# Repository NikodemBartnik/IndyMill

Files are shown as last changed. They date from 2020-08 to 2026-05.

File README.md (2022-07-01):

IndyMill image

IndyMill is an open source DIY CNC machine that is mostly made out of metal. It was designed with simplicity and minimalism in mind! 
This project is not aiming to be the most heavy duty CNC machine out there, it is meant to be easy and inexpensive to build so that anyone can get a hand on precise CNC machining in many materials including metal.
Designed by [Nikodem Bartnik](https://www.youtube.com/nikodembartnik). 

Here are just some of the features of this machine:

  - Aluminium profiles (2080 and 2040)
  - Compatible with Nema17 and Nema23 on X and Y axis (without redesigning a plate Z axis is only compatible with Nema23)
  - Made with ball screws, linear rails and 6mm steel plates to ensure rigidity
  - Can be easily scaled up, you just need to use longer profiles, ballscrews and linear rails

***

### You can find more info at [Indystry.cc](https://indystry.cc/)

***

## Open Source
This machine is open source, so above you can find all of the files that you need to build it. You can also check out videos below to see the build process. As for now, the machine was tested with various kinds of wood, MDF, acrylic and aluminium. It is able to machine all of those materials even with a small 500W spindle.
You can also find more information on my website: [Indystry.cc](https://indystry.cc/indymill/)

## Parts

You can find parts list in PDF or XLSX above but you can also find it here:
  - At [indystry.cc/indymill](https://indystry.cc/indymill) you can find a full table with all needed parts
  - [Google Drive Parts List](https://docs.google.com/spreadsheets/d/19kC1wDViL0N2BjQgnNMfYSCzLNLKAHwQCY5Ngf8wU5I) here you can find an online parts list 
  - You can buy some of the parts on my [store](https://indystry.cc/store/)

## Videos

IndyMill Final test (https://www.youtube.com/watch?v=5jFCecZdbGs)
500W spindle dust shoe (https://www.youtube.com/watch?v=k00IwDHeDQE)
Best upgrades to a CNC machine (https://www.youtube.com/watch?v=VLe03TqoPkM)
Making a CNC drawer (https://www.youtube.com/watch?v=OfrpIvfrLAs)

## Build Instruction
This project is open source so you can find all the files that you need to build it above for free. You can easily build it just by taking a look at some images on my website and my videos.
But if you would like to get a PDF instruction that simplifies the build process, you can easily print it put or it on a smartphone or computer. You can get one through link below and at the same time support my projects! You don't need it but it may help a little :)

### https://gum.co/indymill

### Todos

 - Design a better, bigger cable chain

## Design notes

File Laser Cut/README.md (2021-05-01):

# Laser Cut

These plates can easily be laser cut from steel or aluminium. Steel is  a prefered material as it is stronger and usually cheaper to laser cut. You must shop around for the best price in your country. Also make sure that they are able to cut small holes with a laser, some companies say it's impossible but with a good laser it is easily doable. 
You can also make them on your own with a CNC machine or any other way you want, if you need dimensions just import DXF files to your CAD software and measure whatever you need.
You can also buy the plates in my [store](https://indystry.cc/store/).

DXF files are in `mm`.

| Part | What it looks like |
| --- | --- |
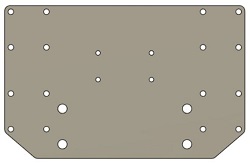
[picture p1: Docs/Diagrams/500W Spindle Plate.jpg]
500W Spindle Plate
| [500W Spindle Plate](500W%20Spindle%20Plate.dxf) |  |
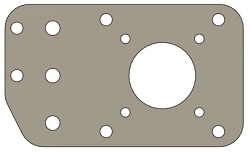
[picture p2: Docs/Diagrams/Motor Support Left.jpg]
Motor Support Left
| [Motor Support Left](Motor%20Support%20Left.dxf) |  |
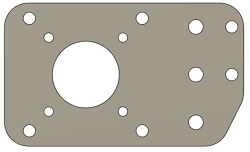
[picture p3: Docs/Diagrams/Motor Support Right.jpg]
Motor Support Right
| [Motor Support Right](Motor%20Support%20Right.dxf) |  |
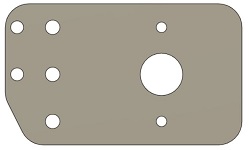
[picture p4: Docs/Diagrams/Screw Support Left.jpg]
Screw Support Left
| [Screw Support Left](Screw%20Support%20Left.dxf) |  |
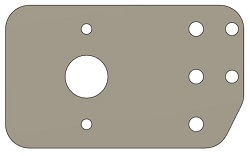
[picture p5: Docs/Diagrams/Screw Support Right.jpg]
Screw Support Right
| [Screw Support Right](Screw%20Support%20Right.dxf) |  |
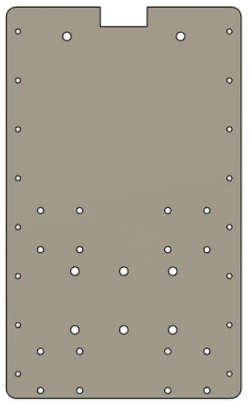
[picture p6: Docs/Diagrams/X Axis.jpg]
X Axis
| [X Axis](X%20Axis.dxf) |  |
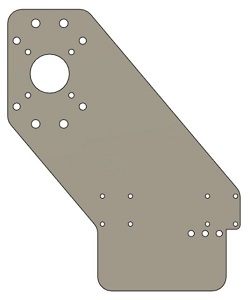
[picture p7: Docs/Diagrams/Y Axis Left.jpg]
Y Axis Left
| [Y Axis Left](Y%20Axis%20Left.dxf) |  |
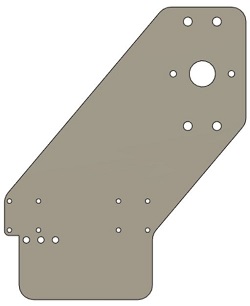
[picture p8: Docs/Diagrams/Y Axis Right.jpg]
Y Axis Right
| [Y Axis Right](Y%20Axis%20Right.dxf) |  |
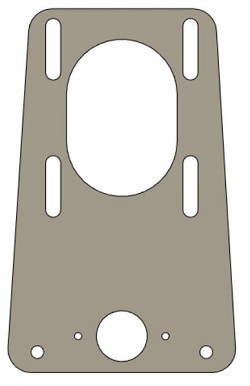
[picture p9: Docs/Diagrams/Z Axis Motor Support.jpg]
Z Axis Motor Support
| [Z Axis Motor Support](Z%20Axis%20Motor%20Support.dxf) |  |
| [Z Axis Rail Support1](Z%20Axis%20Rail%20Support1.dxf) | Z Axis Rail Support1 |
| [Z Axis Rail Support2](Z%20Axis%20Rail%20Support2.dxf) | Z Axis Rail Support2 |

Sometimes people ask me if it is possible to make those plates with different material than metal. It should be possible with thick plywood but obviously machine is not going to be that rigid. 3D printing those plates is most likely not a good idea.
Keep in mind I never tried making those plates out of wood or 3D printing.

Thanks to nice plates images and table to @carlpaton

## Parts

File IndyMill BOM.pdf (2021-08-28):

# List of parts for IndyMill by Nikodem Bartnik

Electronics

Part name | Quantity | BangGood | Aliexpress | Amazon | Comment
Nema23 Stepper motor | 4 | https://bit.ly/2Y0BnrI | https://bit.ly/3iBTGvk | https://amzn.to/3DeE641
IndyShield | 1 | - | - | - | You can buy it here: https://indystry.cc/store/
TB6600 stepper drivers | 4 | https://bit.ly/33VQFSs | https://bit.ly/2PSt2lG | https://amzn.to/3gB2Ycu
Arduino UNO | 1 | https://bit.ly/3gVqtLs | https://bit.ly/2FeDxxo | https://amzn.to/3zo98Uw
Power supply | 1 | https://bit.ly/30RaqZA | https://bit.ly/3kJOtDu | https://amzn.to/2WkwLPR
AC Socket | 1 | https://bit.ly/30Tk2mr | https://bit.ly/30REsfK | https://amzn.to/3mveo5k
Cables | - | https://bit.ly/2PQ2qlc | https://bit.ly/3kH9TBh | -
4 pin connectors | 4 | https://bit.ly/30UUpSi | https://bit.ly/3am7dUU | https://amzn.to/3zm0OVw | I used that to connect stepper motors through electronics case, use other connectors if you want
500W Spindle | 1 | https://bit.ly/3gVpcnx | https://bit.ly/3iCR4NJ | https://amzn.to/3kqVz0z | Choose a spindle that will work best for you. I recommend 500W spindle for beginners, if you are already experienced or not afraid to go BIG go with 1.5kW spindle (that's some serious power!). For 1.5kW spindle you will also need an inverter.
1.5kW Spindle | 1 | https://bit.ly/3kGN4O7 | https://bit.ly/2PMiLHE | https://amzn.to/3mzGw7i
Inverter for 1.5kW Spindle | 1 | https://bit.ly/2E0aHQO
Mechanics
Part name | Quantity | BangGood | Aliexpress | Amazon | Comment
Aluminium profile 20x40 mm 600 mm | 2 | https://bit.ly/3iGGfdM | https://bit.ly/30VoyRv | https://amzn.to/3B9BG4G | You will most likely need to buy longer pieces of aluminium profiles and cut them to a proper length,
| | | | | if you want to build, bigger machine you just have to change lengths of those items, everything else
| | | | | stay the same
Aluminium profile 20x40 mm 666 mm | 2 | https://bit.ly/2XYn3QE | https://bit.ly/3kC0ZoJ | https://amzn.to/3B9BG4G
Aluminium profile 20x80 mm 600 mm | 2 | https://bit.ly/2Y03gQL | https://bit.ly/2PRw7Cs | https://amzn.to/3B9BthU
Trapezoidal lead screw 220 mm | 1 | https://bit.ly/2PS5r4C | https://bit.ly/31Nef0Z | https://amzn.to/3zpXgS4 | Buy longer piece of trapezoidal lead screw and cut to 220mm
Ball Screw SFU1605 650 mm | 1 | https://bit.ly/3fR7yQJ | https://bit.ly/33X9uET | https://amzn.to/3mBfTyM
Ball Screw SFU1605 600 mm | 2 | https://bit.ly/2PQIXkg | https://bit.ly/33X9uET | https://amzn.to/3yeHyrH
Linear Rail MGN12 650 mm | 2 | https://bit.ly/2DSsF85 | https://bit.ly/2XY4ADA | https://amzn.to/2UQD0dp | X axis
Linear Rail MGN12 600 mm | 2 | https://bit.ly/2DSsF85 | https://bit.ly/2XY4ADA | https://amzn.to/3yjJ7o4 | Y axis
Linear Rail MGN12 200 mm | 2 | https://bit.ly/2DSsF85 | https://bit.ly/3fWvn9N | https://amzn.to/3zmz3Mj | Z axis
Linear Rail Block MGN12H | 12 | https://bit.ly/3gVz94w | https://bit.ly/3gVSOBm | https://amzn.to/3zmosBh | If you buy each rail with one block you need just 6 additional blocks (the total of 12)
6000RS bearing | 3 | https://bit.ly/30RjJsl | https://bit.ly/30Uv0by | https://amzn.to/3BtqgsX
6201RS bearing | 6 | https://bit.ly/3h7TWSF | https://bit.ly/2E44Tpj | https://amzn.to/2Y0GRWv
608RS bearing | 1 | https://bit.ly/33Wh6Hz | https://bit.ly/2XYrk6t | https://amzn.to/3kvRVCz
8 to 10mm coupler | 3 | https://bit.ly/30SUCoV | https://bit.ly/3gWQAS3 | https://amzn.to/3gAvYB5 | Make sure that the diameter of the coupler will work with your motor
Closed GT2 Belt 200mm | 1 | https://bit.ly/3aoq69M | https://bit.ly/2Yfwmfl | https://amzn.to/3DgIe3z
GT2 8 mm Pulleys | 2 | https://bit.ly/31Ms1RH | https://bit.ly/31KuTym | https://amzn.to/3BfyXXv
Trapezoidal lead screw lock collar | 3 | https://bit.ly/2Fn9y6E | https://bit.ly/3gVOySf | https://amzn.to/3koSoX7 | That locks the Z axis lead screw in place
Corner connectors | 2 | https://bit.ly/3fVVIVc | https://bit.ly/3kGIdfO | https://amzn.to/3mEnug2
M3x16 mm screws | 14 | https://bit.ly/31QrePG | https://bit.ly/3fUVyh1 | https://amzn.to/3DhWYyZ

You can also buy a kit of screws at https://indystry.cc/store/

M3x10 mm screws | 60 | https://bit.ly/31QrePG | https://bit.ly/2PSy3e0 | https://amzn.to/3Bf5rRQ
M3x8 mm screws | 26 | https://bit.ly/31QrePG | https://bit.ly/30TJGHN | https://amzn.to/3krYgyL
M3 Nut | 4 | https://bit.ly/3DgTkpf | https://bit.ly/3B9NtzS | https://amzn.to/3mCoMIu
M3 T nut | 22 | https://bit.ly/2E5v3rN | https://bit.ly/30WttBP | https://amzn.to/3DkI6jr
M5x20 mm screws | 8 | https://bit.ly/31PSNZh | https://bit.ly/2CnrOvo | https://amzn.to/3mxdEg0
M5x16 mm screws | 22 | https://bit.ly/31PSNZh | https://bit.ly/2CnrOvo | https://amzn.to/3mBVaLs
M5x12 mm screws | 28 | https://bit.ly/31PSNZh | https://bit.ly/2CnrOvo | https://amzn.to/3mx2RT7
M5x10 mm screws | 4 | https://bit.ly/31PSNZh | https://bit.ly/2CnrOvo | https://amzn.to/3jluM6y
M5 T nut | 20 | https://bit.ly/2FnQDIX | https://bit.ly/30WttBP | https://amzn.to/3mBuNW2
M5 nut | 24 | https://bit.ly/31Sl3KX | https://bit.ly/2PSv710 | https://amzn.to/3sN7hGB
M6x12 mm screws | 20 | https://bit.ly/3fWm2yL | https://bit.ly/2E1ev4t | https://amzn.to/3yoLbLr
M12x1 fine thread nut | 3 | - | https://bit.ly/2FhzHDH | https://amzn.to/3mAdhRL

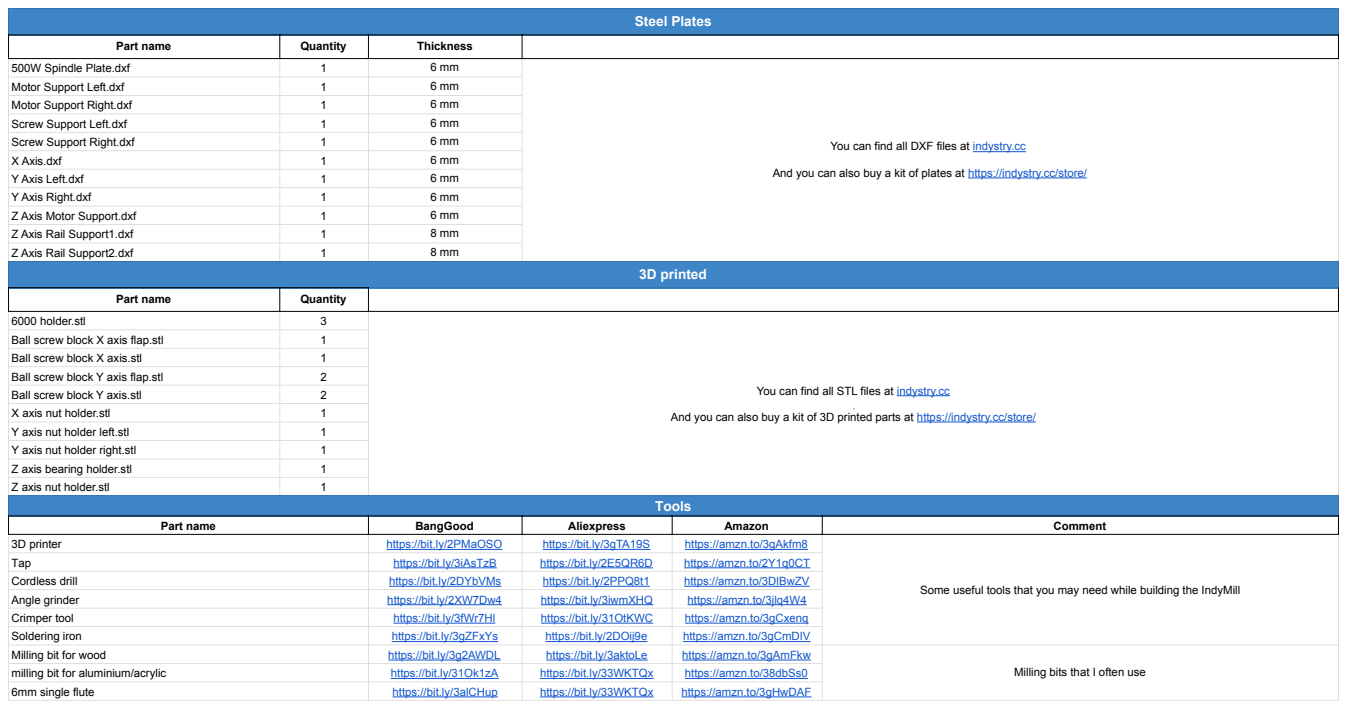
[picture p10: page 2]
Steel Plates; Part name; Quantity; Thickness; 500W Spindle Plate.dxf; Motor Support Left.dxf; Motor Support Right.dxf; Screw Support Left.dxf; Screw Support Right.dxf; X Axis.dxf; Y Axis Left.dxf; Y Axis Right.dxf; Z Axis Motor Support.dxf; Z Axis Rail Support1.dxf; Z Axis Rail Support2.dxf; 3D printed; 6000 holder.stl; Ball screw block X axis flap.stl; Ball screw block X axis.stl; Ball screw block Y axis flap.stl; Ball screw block Y axis.stl; X axis nut holder.stl; Y axis nut holder left.stl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

You can find all DXF files at indystry.cc

And you can also buy a kit of plates at https://indystry.cc/store/

You can find all STL files at indystry.cc

And you can also buy a kit of 3D printed parts at https://indystry.cc/store/

Some useful tools that you may need while building the IndyMill

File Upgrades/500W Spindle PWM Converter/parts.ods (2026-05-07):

Name | Value | Amount | Link
OpAmp LM358DR | - | 1 | https://www.tme.eu/pl/details/lm358dr/wzmacniacze-operacyjne-smd/texas-instruments/ | lub | https://www.tme.eu/pl/details/mcp6h02-e_sn/wzmacniacze-operacyjne-smd/microchip-technology/
Resistor (0603) | 10k | 3
Capacitor (0603) | 10uF | 1

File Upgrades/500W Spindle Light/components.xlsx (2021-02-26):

Name | link | Description
RF-WNMA50DS-ED-N | https://www.tme.eu/pl/details/rf-wnma50ds-ed-n/diody-led-smd-biale/refond/rf-wnma50ds-ed-n-color-zone/ | 5050 LEDs to consider
RF-WNMA50DS-ED-C | https://www.tme.eu/pl/details/rf-wnma50ds-ed-c/diody-led-smd-biale/refond/rf-wnma50ds-ed-c-color-zone/

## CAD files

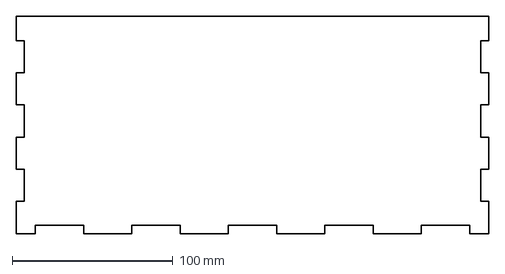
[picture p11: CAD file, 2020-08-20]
Electronics Box/front.dxf
294.0 x 135.0 mm

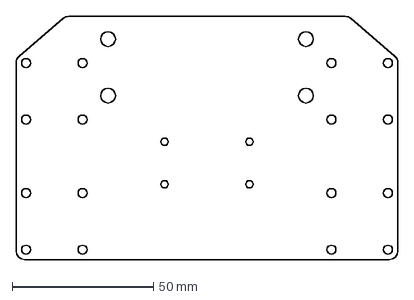
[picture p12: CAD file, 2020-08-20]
Laser Cut/500W Spindle Plate.dxf
135.0 x 86.0 mm

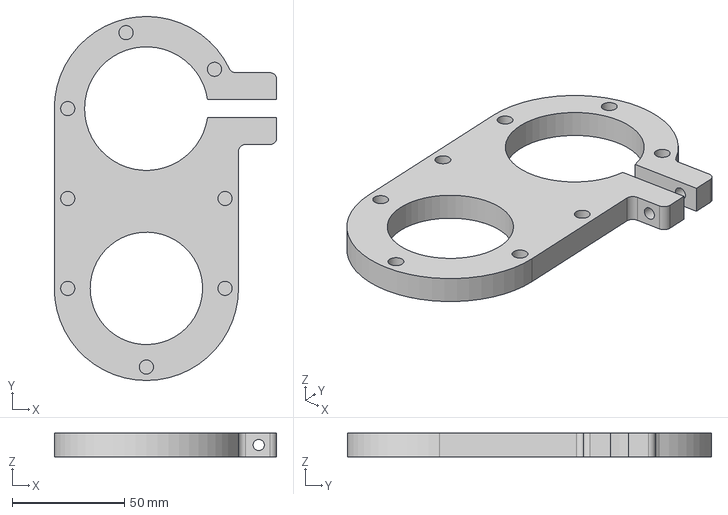
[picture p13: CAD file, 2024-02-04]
Upgrades/Dust Shoe/1.5kw/dust_shoe_top.step
99.0 x 162.0 x 10.5 mm

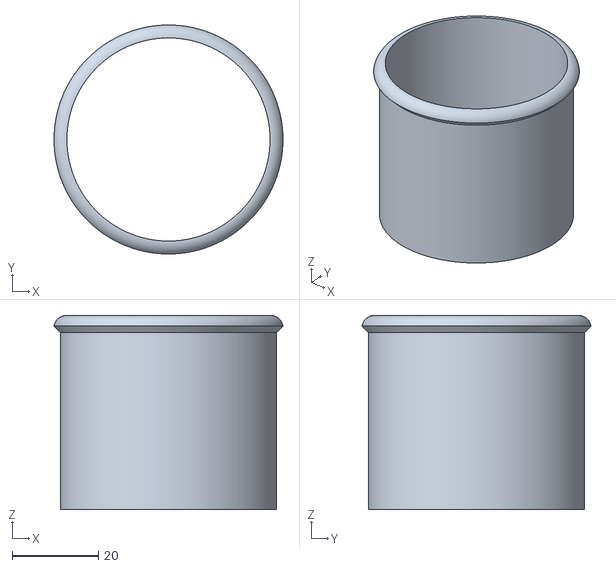
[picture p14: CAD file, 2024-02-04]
Upgrades/Dust Shoe/500w/hose_adapter.stl
53.0 x 53.0 x 45.0

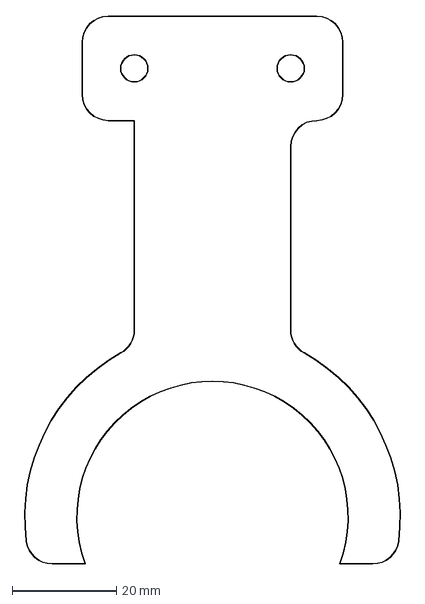
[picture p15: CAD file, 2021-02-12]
Upgrades/Dust Shoe/hose_holder.dxf
75.2 x 105.0 mm

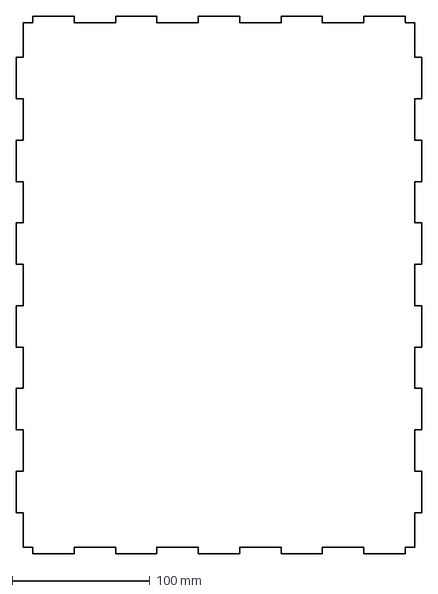
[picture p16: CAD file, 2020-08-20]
Electronics Box/bottom.dxf
294.0 x 390.0 mm

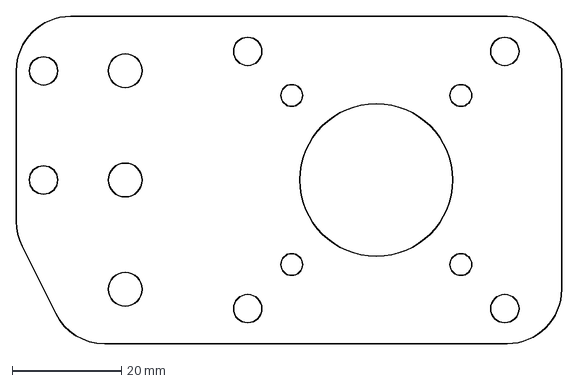
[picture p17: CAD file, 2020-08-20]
Laser Cut/Motor Support Left.dxf
100.0 x 60.0 mm

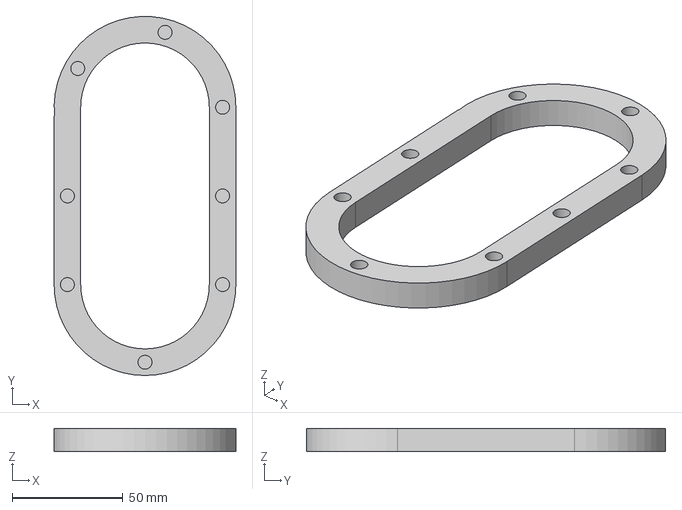
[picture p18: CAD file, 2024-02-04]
Upgrades/Dust Shoe/1.5kw/dust_shoe_bottom.step
82.0 x 162.0 x 10.5 mm

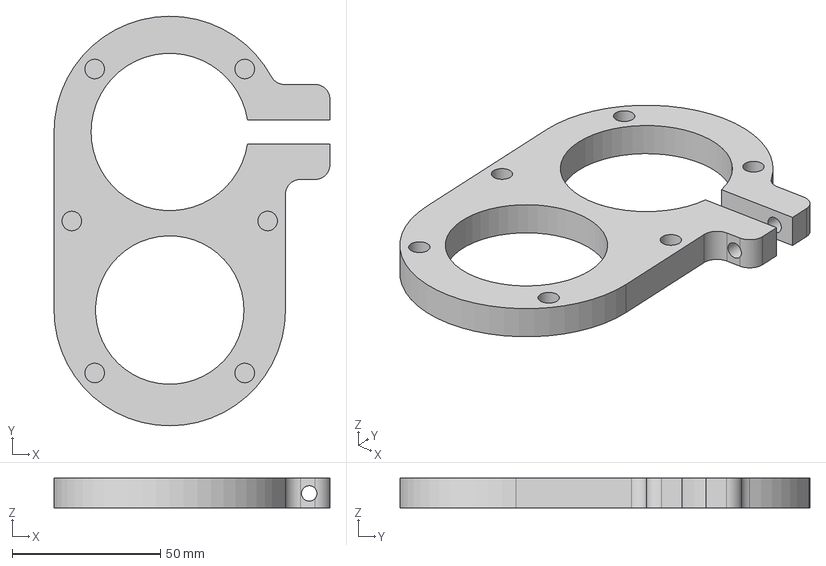
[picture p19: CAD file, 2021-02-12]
Upgrades/Dust Shoe/500w/dust_shoe_top.step
93.0 x 138.0 x 10.0 mm

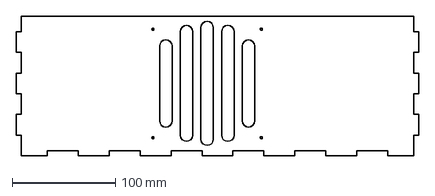
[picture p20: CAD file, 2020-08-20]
Electronics Box/right.dxf
390.0 x 135.0 mm

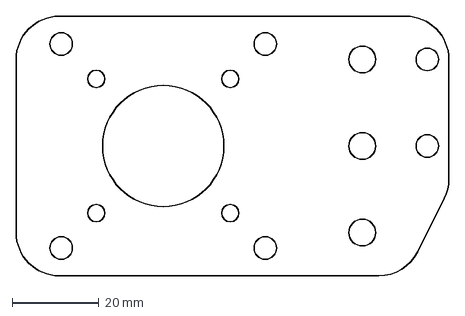
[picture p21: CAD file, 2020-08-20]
Laser Cut/Motor Support Right.dxf
100.0 x 60.0 mm

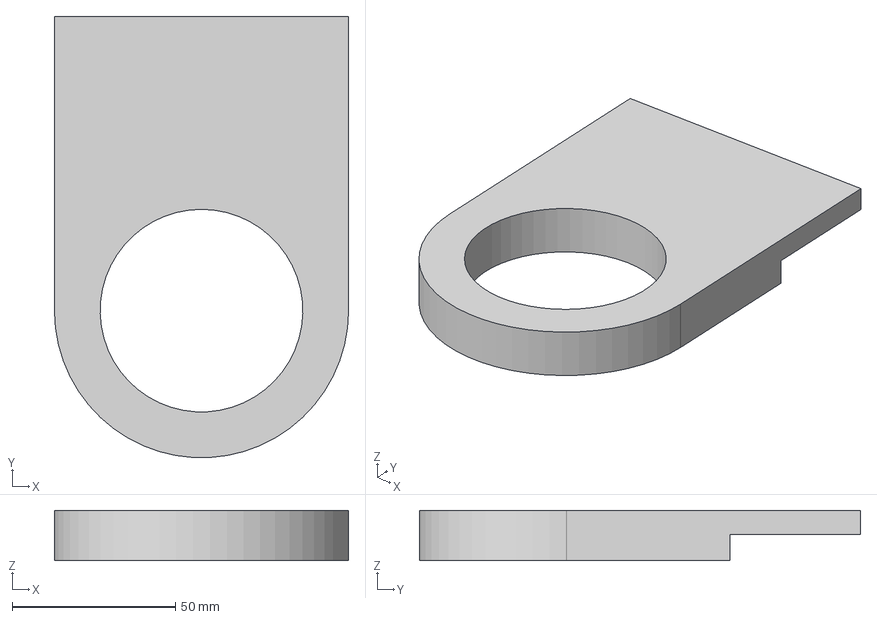
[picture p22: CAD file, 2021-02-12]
Upgrades/Dust Shoe/500w/adapter_holder.step
90.0 x 134.9 x 15.4 mm

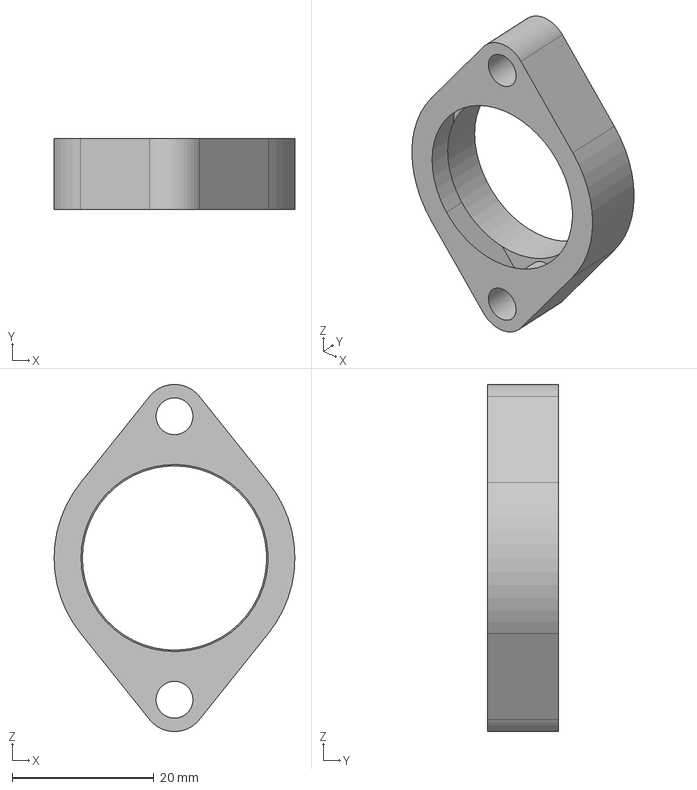
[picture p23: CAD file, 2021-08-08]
3D Printed/STEP/6000 holder.step
34.0 x 10.0 x 49.0 mm

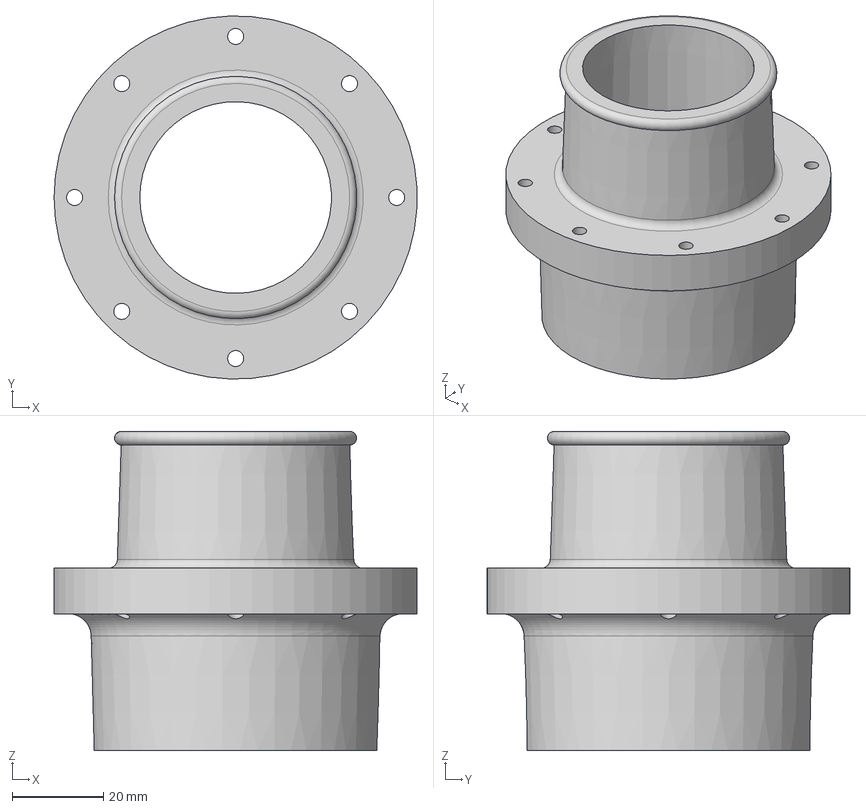
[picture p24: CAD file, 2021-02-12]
Upgrades/Dust Shoe/1.5kw/hose_vacuum_adapter.step
79.5 x 79.6 x 70.0 mm

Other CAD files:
3D Printed/STEP/Z axis bearing holder.step
3D Printed/6000 holder.stl
3D Printed/Ball screw block X axis flap.stl
3D Printed/Ball screw block X axis.stl
3D Printed/Ball screw block Y axis flap.stl
3D Printed/Ball screw block Y axis.stl
3D Printed/DIY ball screw cover/1.stl
3D Printed/DIY ball screw cover/2.stl
3D Printed/DIY ball screw cover/3.stl
3D Printed/DIY ball screw cover/4.stl
3D Printed/Limit switch holder.stl
3D Printed/STEP/Ball screw block X axis.step
3D Printed/STEP/Ball screw block Y axis.step
3D Printed/STEP/Limit switch holder.step
3D Printed/STEP/X axis nut holder.step
3D Printed/STEP/Y axis ball screw holder.step
3D Printed/STEP/Y axis nut holder left.step
3D Printed/STEP/Y axis nut holder right.step
3D Printed/STEP/Z axis nut holder.step
3D Printed/X axis nut holder.stl
3D Printed/Y axis nut holder left.stl
3D Printed/Y axis nut holder right.stl
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

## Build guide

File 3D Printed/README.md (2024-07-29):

# 3D printed
Yes, 3D printed parts are definitely strong enough for such a CNC machine. I use 3 perimeters and 40% infill to print those parts out of PLA, PETG is also a good choice. Above you can find STL files and STEP files in case you want to modify something.
You can also buy 3D printed parts in my [store](https://indystry.cc/store/).

| Part | What it looks like | Amount needed |
| --- | --- | --- |
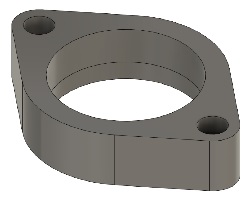
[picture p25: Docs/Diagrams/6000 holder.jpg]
6000 holder
| [6000 holder](6000%20holder.stl) |  | 3 |
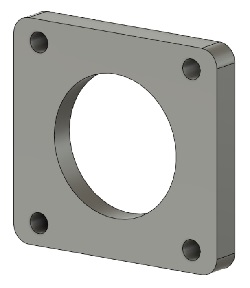
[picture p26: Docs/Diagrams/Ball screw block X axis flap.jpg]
Ball screw block X axis flap
| [Ball screw block X axis flap](Ball%20screw%20block%20X%20axis%20flap.stl) |  | 1
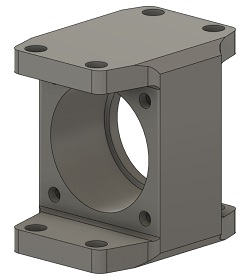
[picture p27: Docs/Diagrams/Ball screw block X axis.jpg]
Ball screw block X axis
| [Ball screw block X axis](Ball%20screw%20block%20X%20axis.stl) |  | 1
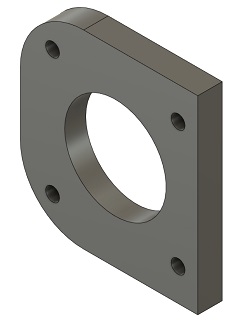
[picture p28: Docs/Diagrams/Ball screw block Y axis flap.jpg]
Ball screw block Y axis flap
| [Ball screw block Y axis flap](Ball%20screw%20block%20X%20axis%20flap.stl) |  | 2
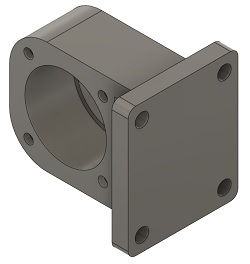
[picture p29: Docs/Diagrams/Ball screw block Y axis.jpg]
Ball screw block Y axis
| [Ball screw block Y axis](Ball%20screw%20block%20Y%20axis.stl) |  | 2
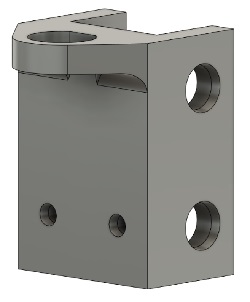
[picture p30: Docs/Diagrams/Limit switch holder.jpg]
Limit switch holder
| [Limit switch holder](Limit%20switch%20holder.stl) |  | 3
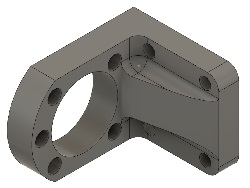
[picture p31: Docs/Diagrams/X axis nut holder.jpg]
X axis nut holder
| [X axis nut holder](X%20axis%20nut%20holder.stl) |  | 1
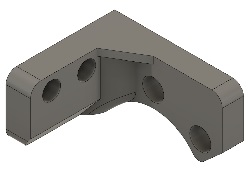
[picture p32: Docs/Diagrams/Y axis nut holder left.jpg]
Y axis nut holder left
| [Y axis nut holder left](Y%20axis%20nut%20holder%20left.stl) |  | 1
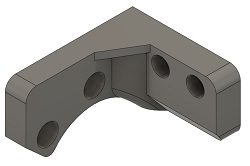
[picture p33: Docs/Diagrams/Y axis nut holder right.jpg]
Y axis nut holder right
| [Y axis nut holder right](Y%20axis%20nut%20holder%20right.stl) |  | 1
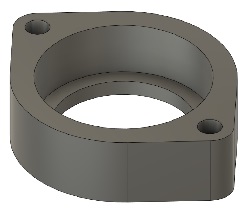
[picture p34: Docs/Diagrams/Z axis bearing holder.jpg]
Z axis bearing holder
| [Z axis bearing holder](Z%20axis%20bearing%20holder.stl) |  | 1
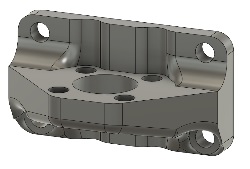
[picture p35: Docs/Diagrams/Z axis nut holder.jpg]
Z axis nut holder
| [Z axis nut holder](Z%20axis%20nut%20holder.stl) |  | 1

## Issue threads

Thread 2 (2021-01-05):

STEP Files?

GaryFlowers, 2021-01-05:
Hello, can you upload the machine assembly STEP files here on GIT? I would like to get measurements off the frame and other parts but I don't see any STEP files like the Dremel CNC.

PS, keep up the awesome work, and thank you for sharing your projects!

NikodemBartnik, 2022-01-02:
There are STEP files for 3D printed parts and DXF for the plates, based on that you can create your own assembly that will suit your needs

Closed 2022-01-02.

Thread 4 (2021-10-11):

500W Spindle PWM Converter

MarkedOne, 2021-10-11:
The text states it's for a 0-10v signal. However in the video and other media, it blows on 0-10v. you changed it in the video for 0-5v, is the silkscreen text incorrect?

Closed 2022-01-02.

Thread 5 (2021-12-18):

1.5KW mounting plate

jack9603301, 2021-12-18:
Hello, I saw the installation plate of 500W, but I didn't see the installation plate of 1.5KW spindle. Where is it?

NikodemBartnik, 2021-12-20:
There is too many different version of 1.5kW spindle and it's just not possible to design a single plate that will work with all (or at least most) spindles. As you can see in this video: https://www.youtube.com/watch?v=VLe03TqoPkM
I drilled some additional holes in 500W plate to mount the new spindle. You can also just import the DXF file to any CAD software and easily edit the 500W spindle plate to get it working with your spindle.

Closed 2022-01-02.

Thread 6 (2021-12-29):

Full 3D model?

eyesonlybob, 2021-12-29:
Awesome project! I don't see a full 3D model available. Can you add one? I'm interested in building one but want to inspect the assembly closer first.

Kosh42, 2022-01-02:
What I was after too. To be fully Open Source, the source should also be available to inspect, and adapt. Otherwise free to build is possibly more accurate description.

Still an awesome project. I just want to scale it down for my needs.

NikodemBartnik, 2022-01-02:
You can find all the STEP files for 3D printed parts and DXF for the plates, based on that you can create your own assembly that will suit your needs and modify whatever you want. That is the source of the project

eyesonlybob, 2022-01-02:
That just makes things more difficult than it needs to be.  You're limiting
further development of indymill by not releasing the full model.

On Sun, Jan 2, 2022 at 5:34 AM Nikodem Bartnik ***@***.***>
wrote:

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

Closed 2022-01-02.

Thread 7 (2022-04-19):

I have a question. Has the author of indymill considered using LinuxCNC to control this CNC?

jack9603301, 2022-04-19:
I have a question. Has the author of indymill considered using LinuxCNC to control this CNC?

It should be better and have strong scalability. Of course, you need SBC or industrial computer for system integration. It looks close to a truly sophisticated device.. Raspberry PI and orange PI offer new possibilities. Of course, it depends on the specific individual who built the CNC (anyway, indymill is just a prototype of mechanical CNC system design. So is the author. I'm just curious.

NikodemBartnik, 2022-04-21:
I never tried using LinuxCNC, I am quite happy with GRBL on my machine and have no need for that. As you mentioned that's not a part of the IndyMill project, you can use anything you want to control this machine.

jack9603301, 2022-04-23:
thanks

Closed 2023-01-04.

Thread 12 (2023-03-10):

Full Fusion 360 Model

stefanspurgin91, 2023-03-10:
Hi, i saw that you answered on a few questions about full 3D model, that we can to use some files, but full model has all, linear modules, aluminium profiles, screws and other stuff. Are you consider to share full 3D model only with Patreon supporters starting from lets say package 2(not the cheapest one). It will be very useful for inspections and customization, i want to build your machine. If some people support you on Ptreon+buy your pdf instruction+order your Indy shield, in my opinion, that people maybe deserve to get fully model via mail, or some link to full 3D model with complete machine. Project is now about 3 years old and you arecprobably working on the new one. I dont see why not to share with patreon supporters at least. Best Regards

NikodemBartnik, 2023-04-03:
There are all the files available in case you want to replicate the machine. You can easily extrude DXF files to the thickness you need and import STEP files of the 3D printed files. Complete 3D assembly is not publicly available

Closed 2023-04-03.

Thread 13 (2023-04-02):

Spindle PWM  and Light PCBs - can't open them (plus additional questions)

FSXLiveriesdotcom, 2023-04-02:
Hi @NikodemBartnik
I have problems with opening SCH and BRD files.
I tried to open SCH direcly in Eagle (and directly import in Fusion eCAD) but got error:

 **_Loading Y:/Downloads/spindle_light.sch ...
Error:
line 9, column 129: This is not an EAGLE file._**

Same error happens when trying PWM controller files.
EasyEDA and KiCAD also can't import them.

Plus I have additional questions as some things are confusing. I must admit,  my understanding of electronics here might be a issue here.

I uploaded controller gerber files to JLCPBCB to at least see 3D design and try to recreate the PCB from scratch.
1. It seems that apart from resistors and capacitor, there is only one other component - amplifier LM358DR
   However, in BOM file there is also mentioned voltage regulator which doesn't have any placement on PCB.
   Am I missing something?
2. Also,  could you make some simple drawing to show up how to connect spindle > PCB > PSU?
   Similar pic to one you have done for stepper motors and drivers. That would be very useful.

3. Why there are pin additional pin headers on PWM PCB?  What is their purpose?

Greetings, Mark

NikodemBartnik, 2023-04-03:
All the files open perfectly fine for me (I am using Eagle 9.5.1).
The voltage regulator is an old part that in the end wasn't used in the project.
The pin headers are there in case you prefer to connect it with breadboard cables instead of screw terminals

FSXLiveriesdotcom, 2023-04-20:
Hey Nikodem.
OK, I tried once more and was able to open the files but only after downloading .zip of the entire repo.
When tried first time I was downloading single files only.

Closed 2023-04-20.

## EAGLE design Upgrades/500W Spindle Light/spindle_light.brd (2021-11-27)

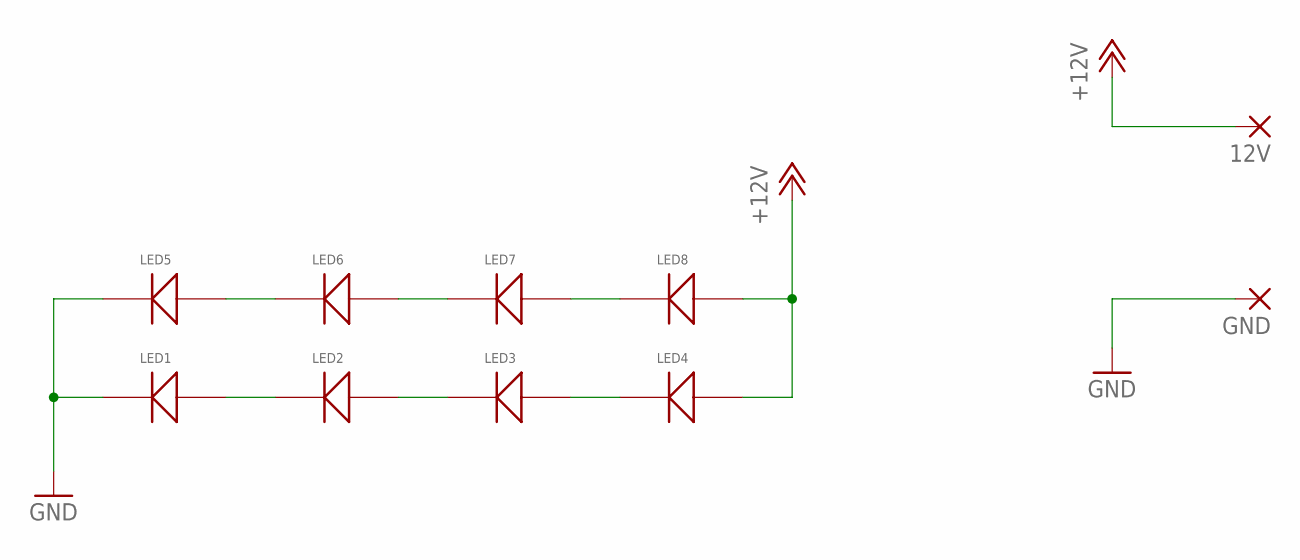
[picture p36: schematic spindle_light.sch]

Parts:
12V: SMD5; SMD2,54-5,08
GND: SMD5; SMD2,54-5,08
LED1, LED2, LED3, LED4, LED5, LED6, LED7, LED8: RF-45HA50DS-EE-Y; 5050LED

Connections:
+12V: 12V.1, LED4.P$4, LED4.P$5, LED4.P$6, LED8.P$4, LED8.P$5, LED8.P$6
GND: GND.1, LED1.P$1, LED1.P$2, LED1.P$3, LED5.P$1, LED5.P$2, LED5.P$3
unnamed: LED5.P$4, LED5.P$5, LED5.P$6, LED6.P$1, LED6.P$2, LED6.P$3
unnamed: LED1.P$4, LED1.P$5, LED1.P$6, LED2.P$1, LED2.P$2, LED2.P$3
unnamed: LED2.P$4, LED2.P$5, LED2.P$6, LED3.P$1, LED3.P$2, LED3.P$3
unnamed: LED6.P$4, LED6.P$5, LED6.P$6, LED7.P$1, LED7.P$2, LED7.P$3
unnamed: LED7.P$4, LED7.P$5, LED7.P$6, LED8.P$1, LED8.P$2, LED8.P$3
unnamed: LED3.P$4, LED3.P$5, LED3.P$6, LED4.P$1, LED4.P$2, LED4.P$3

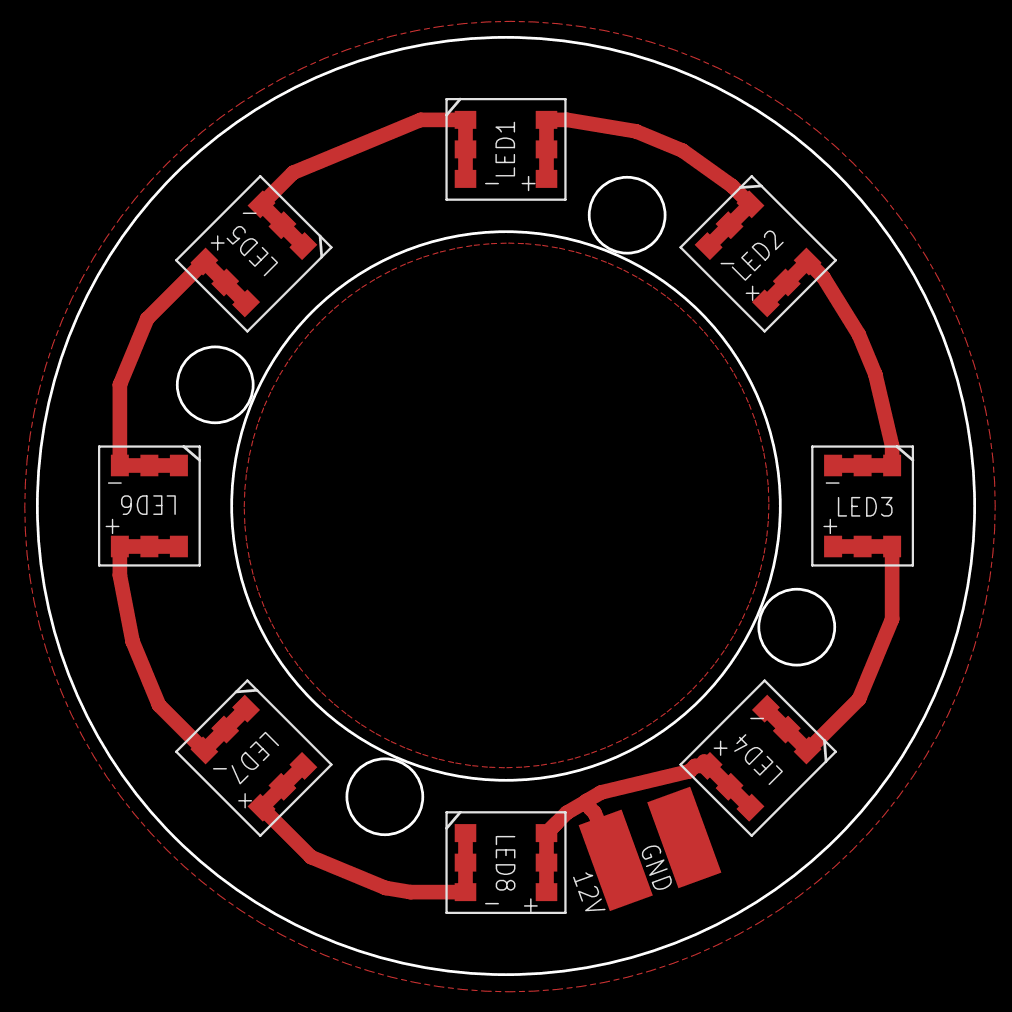
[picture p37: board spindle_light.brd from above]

Board: 2 copper layers, 52.1 x 52.1 mm, 10 parts (0 on the bottom side), 8 nets.

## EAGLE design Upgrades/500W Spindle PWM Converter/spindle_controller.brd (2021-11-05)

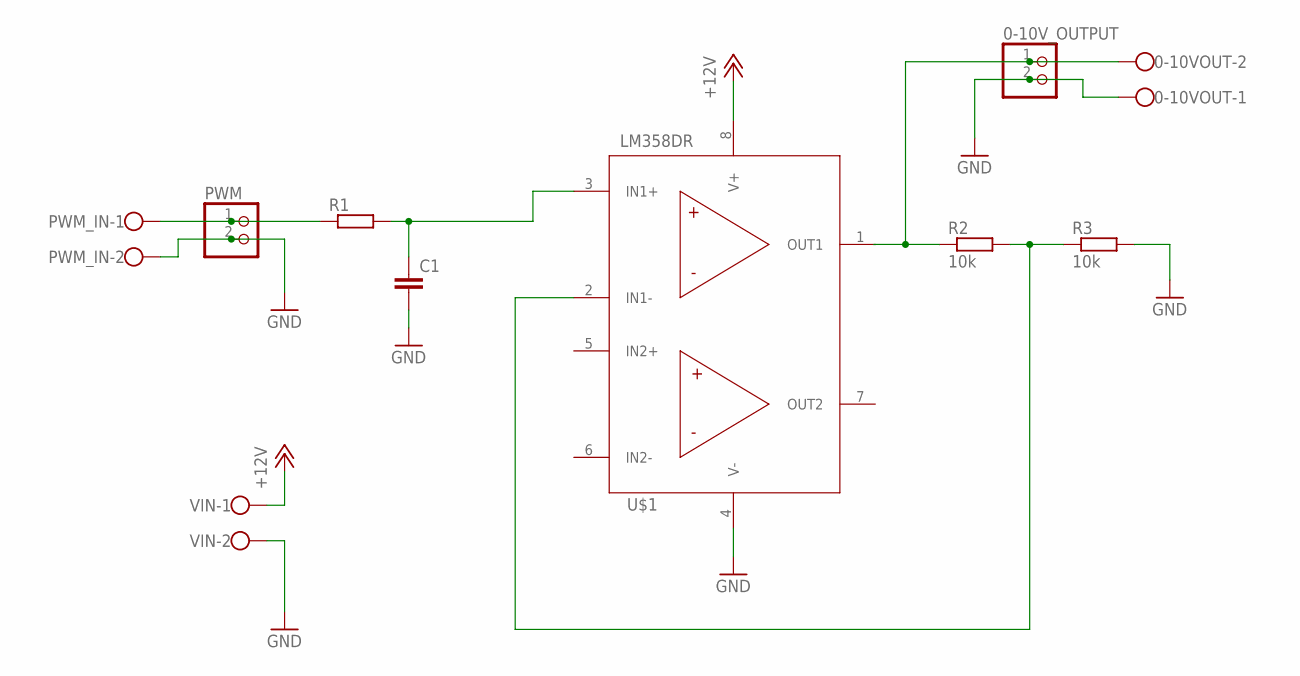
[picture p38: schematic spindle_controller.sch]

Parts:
0-10VOUT: W237-102
0-10V_OUTPUT: PINHD-1X2; 1X02
C1: C-EUC0603; C0603
PWM: PINHD-1X2; 1X02
PWM_IN: W237-102
R1: R-EU_R0603; R0603
R2, R3: 10k; R0603
U$1: LM358DRLM358DR_SOIC8; SOIC127P599X175-8N
VIN: W237-102

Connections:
+12V: U$1.8 (V+), VIN.1
GND: 0-10VOUT.1, 0-10V_OUTPUT.2, C1.2, PWM.2, PWM_IN.2, R3.2, U$1.4 (V-), VIN.2
unnamed: PWM.1, PWM_IN.1, R1.1
unnamed: C1.1, R1.2, U$1.3 (IN1+)
unnamed: R2.2, R3.1, U$1.2 (IN1-)
unnamed: 0-10VOUT.2, 0-10V_OUTPUT.1, R2.1, U$1.1 (OUT1)

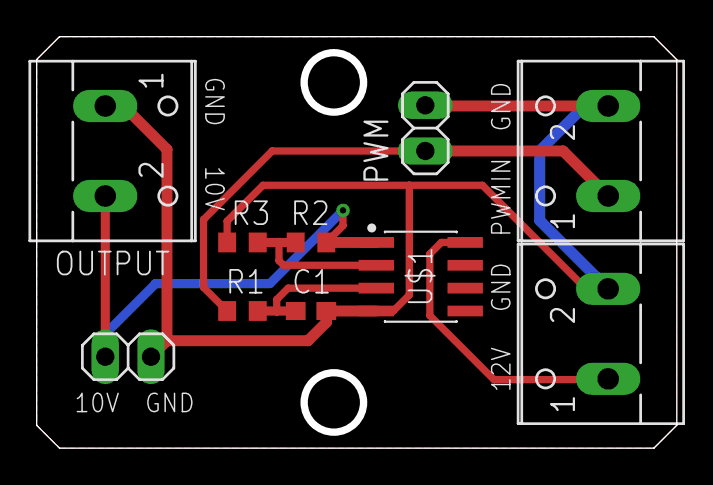
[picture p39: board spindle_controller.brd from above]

Board: 2 copper layers, 35.6 x 22.9 mm, 10 parts (0 on the bottom side), 6 nets.

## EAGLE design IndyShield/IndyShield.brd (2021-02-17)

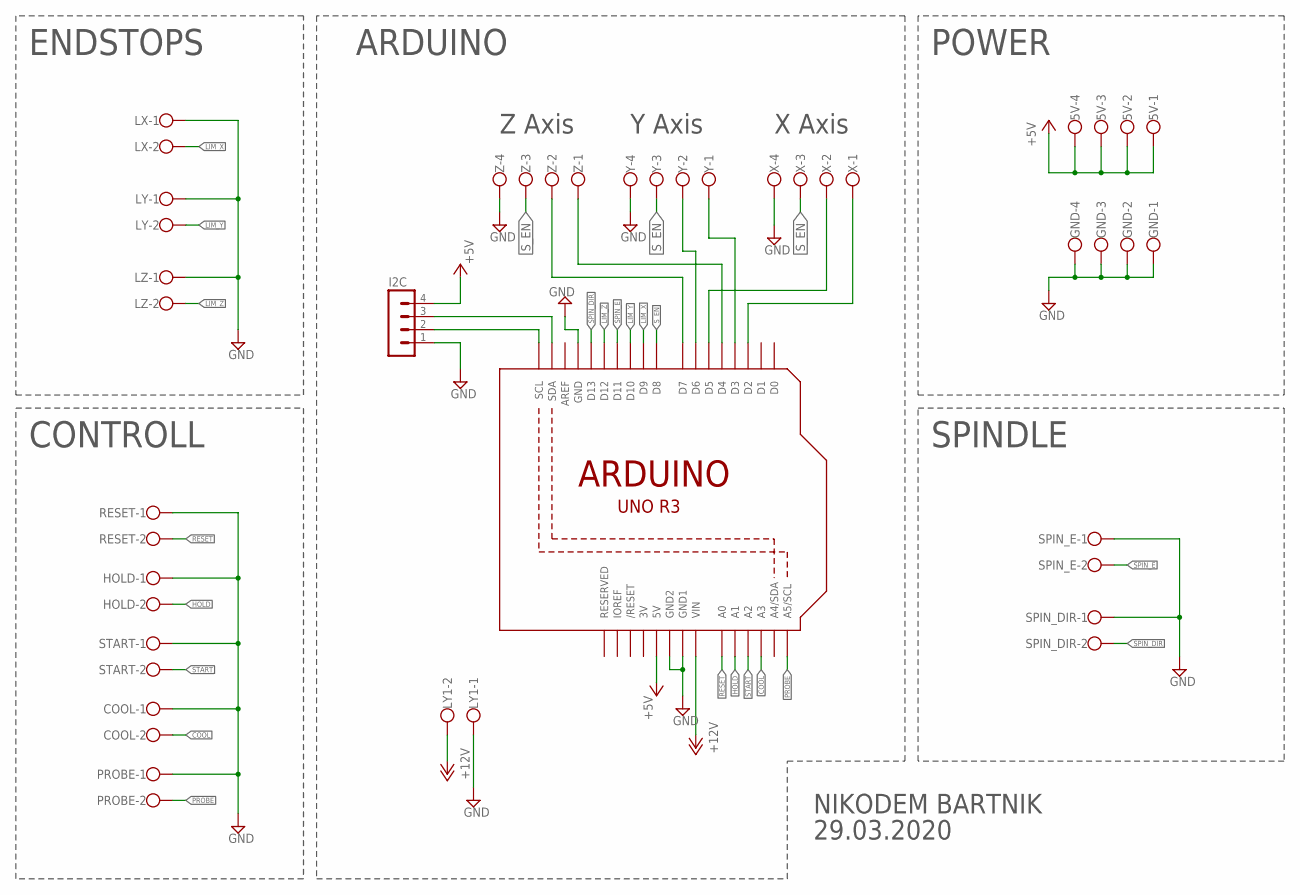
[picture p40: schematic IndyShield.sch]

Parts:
5V: W237-4
COOL: W237-102
GND: W237-4
HOLD: W237-102
I2C: MA04-1
LX: W237-102
LY, LY1: W237-102
LZ: W237-102
PROBE: W237-102
RESET: W237-102
SPIN_DIR: W237-102
SPIN_E: W237-102
START: W237-102
U1: ARDUINOR3-BPLACE
X: W237-4
Y: W237-4
Z: W237-4

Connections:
3V: U1.3V
+5V: 5V.1, 5V.2, 5V.3, 5V.4, I2C.4, U1.5V
+12V: LY1.2, U1.VIN
COOL: COOL.2, U1.A3
GND: COOL.1, GND.1, GND.2, GND.3, GND.4, HOLD.1, I2C.1, LX.1, LY.1, LY1.1, LZ.1, PROBE.1, RESET.1, SPIN_DIR.1, SPIN_E.1, START.1, U1.GND, U1.GND1, U1.GND2, X.4, Y.4, Z.4
HOLD: HOLD.2, U1.A1
LIM_X: LX.2, U1.D9
LIM_Y: LY.2, U1.D10
LIM_Z: LZ.2, U1.D12
unnamed: U1.D5, X.2
unnamed: U1.D2, X.1
unnamed: U1.D6, Y.2
unnamed: U1.D3, Y.1
unnamed: U1.D7, Z.2
unnamed: U1.D4, Z.1
unnamed: I2C.3, U1.SDA
unnamed: I2C.2, U1.SCL
PROBE: PROBE.2, U1.A5 (A5/SCL)
RESET: RESET.2, U1.A0
SPIN_DIR: SPIN_DIR.2, U1.D13
SPIN_E: SPIN_E.2, U1.D11
START: START.2, U1.A2
S_EN: U1.D8, X.3, Y.3, Z.3

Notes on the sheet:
X Axis
Y Axis
Z Axis
ENDSTOPS
SPINDLE
ARDUINO
POWER
CONTROLL
NIKODEM BARTNIK
29.03.2020

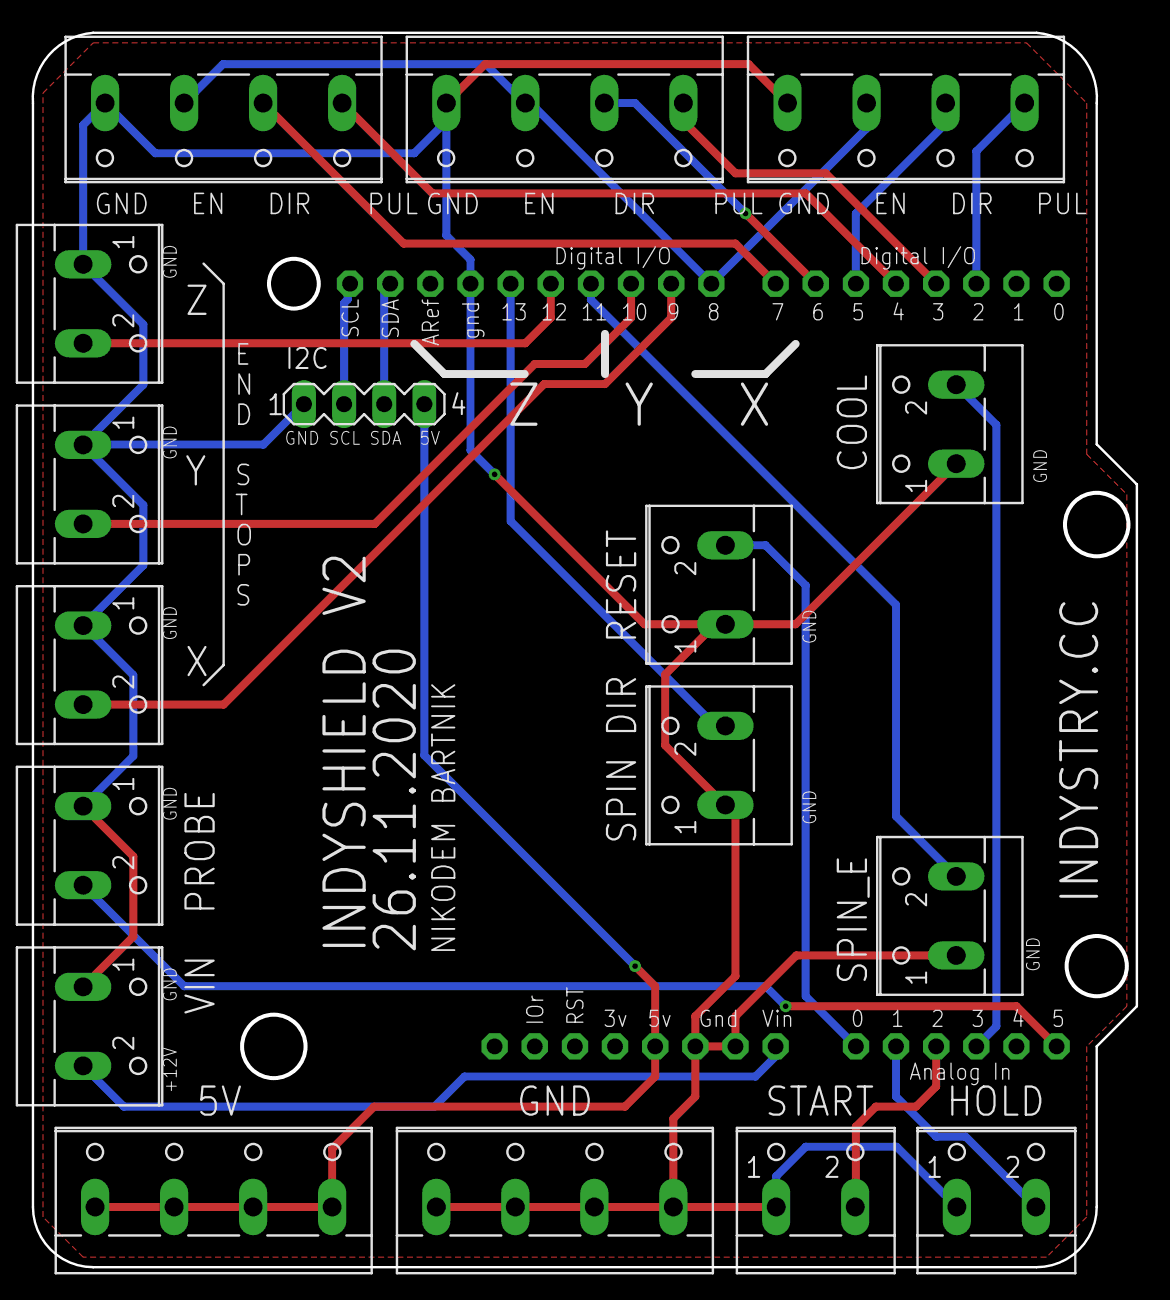
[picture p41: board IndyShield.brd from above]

Board: 2 copper layers, 69.9 x 78.1 mm, 18 parts (0 on the bottom side), 22 nets.

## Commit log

2020-08-20 First commit
    First commit of all design files, PCB schematic and layout, electronics box and some other useful things
    [500W Spindle Plate.dxf, 6000 holder.stl, IndyMill BOM.xlsx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]
2020-10-08 Ball screw covers STL
    Add balscrew covers STL files, small changes to some STL files
    [1.stl, 2.stl, 3.stl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]
2021-02-12 Added dust shoe files
    [IndyMill_dust_shoe_bottom.step, IndyMill_dust_shoe_top.step, adapter_holder.step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]
2021-02-17 Updated IndyShield to V2
    Swapped Z axis limit with spindle enable as it should be for current version of GRBL
    [IndyShield.brd, IndyShield.sch]
2021-03-20 Smaller number of LEDs to make it a bit less bright
    Everything connected and prototyped working fine so far. Need to check the dimensions
    [spindle_light.brd, spindle_light.sch]
2021-04-13 Laser cut part diagrams
2021-08-08 Redesign of 3D printed parts
    [Ball screw block X axis flap.stl, Ball screw block X axis.stl, Ball screw block Y axis flap.stl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]
2021-08-08 Added STEP files of all printed parts
    [6000 holder.step, Ball screw block X axis.step, Ball screw block Y axis.step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]
2021-08-28 Updated BOM
    [IndyMill BOM.xlsx]
2021-08-29 Added 500W spindle light and PWM converter. Also some clean up
    [IndyMill_dust_shoe_bottom.step, IndyMill_dust_shoe_top.step, adapter_holder.step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]
2021-08-30 Spindle light update
    [spindle_light.brd, spindle_light.sch]
2021-10-24 Redesign spindle light
    [spindle_light.brd]
2021-10-24 Squashed commit of the following:
    commit a86822d2883ca98a5418853accf885b86f3b1a4e
    Author: NikodemBartnik <nikodem.bartnik@gmail.com>
    Date: Sun Oct 24 13:37:13 2021 +0200
    typo fix
    commit 9fb647f2a9ac5ded72f7a5d88a2245ac32e2f947
    Author: NikodemBartnik <nikodem.bartnik@gmail.com>
    Date: Sun Oct 24 13:33:07 2021 +0200
    Add 3D printed parts images, new main picture
2021-11-05 Clean up and new production files
    [spindle_controller.brd, spindle_light.brd]
2021-11-27 GND error fix
    [spindle_light.brd, spindle_light.sch]
2022-02-08 Bigger X axis nut holder
    [X axis nut holder.step, X axis nut holder.stl]
2023-06-25 fix 3D printer friendly X axis block
    [Ball screw block X axis.step, Ball screw block X axis.stl]
2024-02-04 update dust shoe
    [adapter_holder.step, dust_shoe_bottom.step, dust_shoe_top.step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]
